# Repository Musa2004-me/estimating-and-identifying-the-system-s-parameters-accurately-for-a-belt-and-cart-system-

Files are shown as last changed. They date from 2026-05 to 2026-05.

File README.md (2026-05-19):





https://github.com/user-attachments/assets/3bb75c5b-a4b6-444a-98ba-ffa4dd2a95e5

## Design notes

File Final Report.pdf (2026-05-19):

AIN SHAMS UNIVERSITY-FACULTY OF ENGINEERING

### [MCT234s]

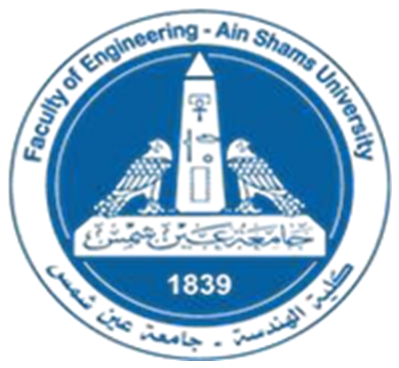
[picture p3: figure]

### Modeling and Simulation of Mechatronics systems

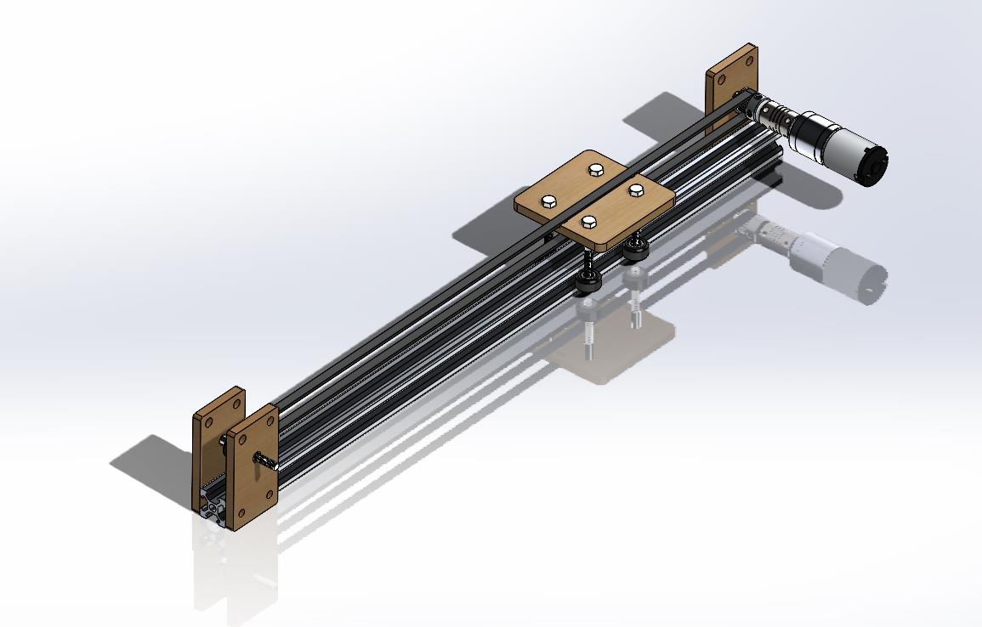
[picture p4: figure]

## TEAM 8

Name | ID | Section
Abdelkarim Wael Abdelkarim | 2101733 | 1 MCT
Mahmoud Salama Mohamed Abdo | 2100961 | 1 MCT
Abdullah Mahmoud Abdelkarim | 2100658 | 1 MCT
Musa Gamal El-Shenawy | 2100614 | 1 MCT

### Table of Contents

### Table of figures

### ABSTRACT

This work presents the creation of a simulation model for a belt-and-cart system using SolidWorks, Simulink, and MATLAB. The primary goal is to estimate and identify the system's parameters accurately, including mass, damping coefficients (incorporating friction), and belt tension characteristics. The belt-and-cart system is widely utilized in mechanical applications and requires precise modelling to understand its dynamic behaviour.

The simulation model is developed by integrating a 3D mechanical design from SolidWorks with Simulink for dynamic analysis. MATLAB is employed for numerical computations and parameter extraction. The damping coefficients account for frictional effects, which are crucial for realistic modelling. The model considers key elements such as the belt's elasticity, cart inertia, and interactions between the belt and pulley system. Parameter estimation is achieved by comparing simulated outputs with experimental data or predefined system behaviours.

The proposed approach provides an efficient framework for studying the dynamics of belt-and-cart systems, enabling accurate parameter determination without requiring extensive physical testing. This model serves as a foundation for further studies, including control system design and optimization of similar mechanical systems.

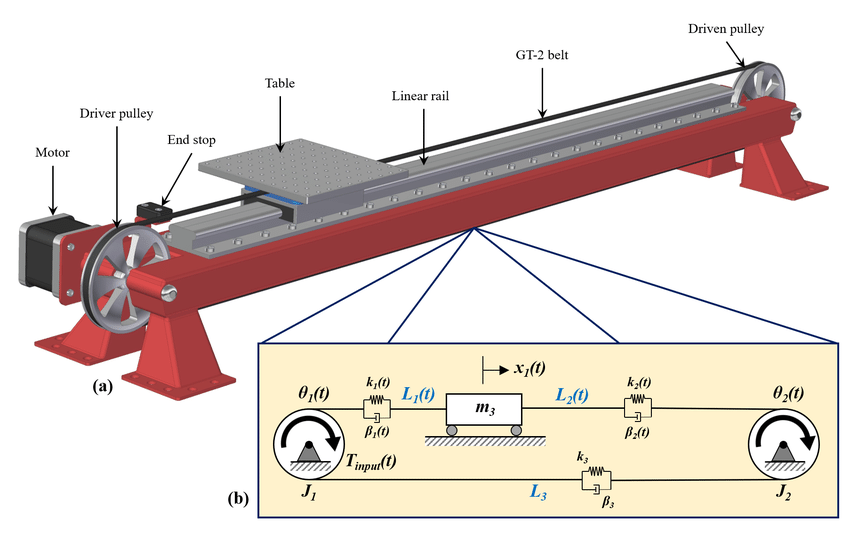
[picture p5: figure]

### INTRODUCTION

Parameter estimation is a process in which the key parameters of a system are identified by comparing its observed behavior to a mathematical or simulated model. This technique is widely used in engineering and science to fine-tune models for greater accuracy, enabling better predictions and control of system performance. In mechanical systems, parameter estimation helps determine values such as mass, damping coefficients, and stiffness, which are often challenging to measure directly but are critical for understanding system dynamics.

Simulink, a MATLAB-based simulation environment, is an essential tool for modelling, simulating, and analysing dynamic systems. It provides a graphical interface for building models using blocks that represent mathematical functions, physical components, and signal processing operations. Simulink is widely used in academia and industry for designing and testing systems ranging from mechanical to electrical and control systems, making it ideal for studying the dynamics of a belt-and-cart system.

In this project, we focus on developing a simulation model of a belt-and-cart system using Simulink to estimate its critical parameters. The system consists of a cart driven by a belt-and-pulley mechanism, with dynamics influenced by factors such as mass, belt tension, and damping (including friction). By creating an accurate model and performing parameter estimation, we aim to replicate the system’s behavior and gain deeper insights into its characteristics. This project serves as a hands-on application of parameter estimation techniques and demonstrates the power of Simulink in solving real-world engineering problems.

### Objective:

- to develop a simulation model for a belt-and-cart system using Simulink
- to estimate the system's key parameters accurately. This includes determining parameters such as cart mass, damping coefficients (accounting for friction), and belt stiffness, which are essential for predicting the system's dynamic behavior.

The project aims to:

- Build a comprehensive simulation model in Simulink, integrating the dynamics of the belt, cart, and pulley system.
- Utilize parameter estimation techniques to align the simulation results with experimental or theoretical data, ensuring the model accurately reflects the real system.
- Validate the estimated parameters by comparing the simulated outputs with observed system behavior, demonstrating the reliability of the simulation.
- Through this approach, the project highlights the importance of combining simulation tools like Simulink with parameter estimation methodologies to analyse, design, and optimize mechatronic systems effectively

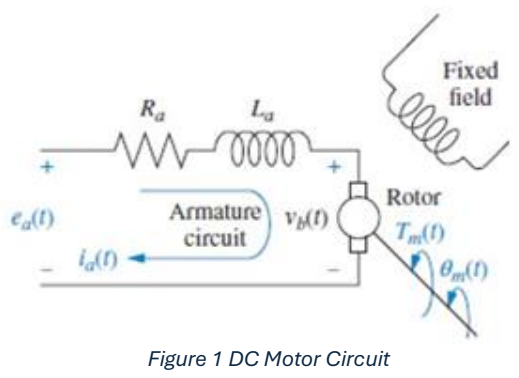
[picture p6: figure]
Figure 1 DC Motor Circuit

### Mathematical Model of the System:-

1-Electrical equation:-

Ea=(Ra+LS)Ia(s)+ Kbω

Vin=Ea
2-Mechanical model

Jω̇ = Tm −Tdamping −Tstatic → Neglecting initial condition(static torque)

Tm =kt ×Ia(s)

Tdamping = Beq × ω

JeqS ω = kt× Ia(s)− Deq × ω
Deq=Dm+Dmech.sys
Jeq=Jm+Jmech.sys
Transfer Function:-

ω
Vin =

1
R
Kt (S²Jeq + DeqS) + SKb

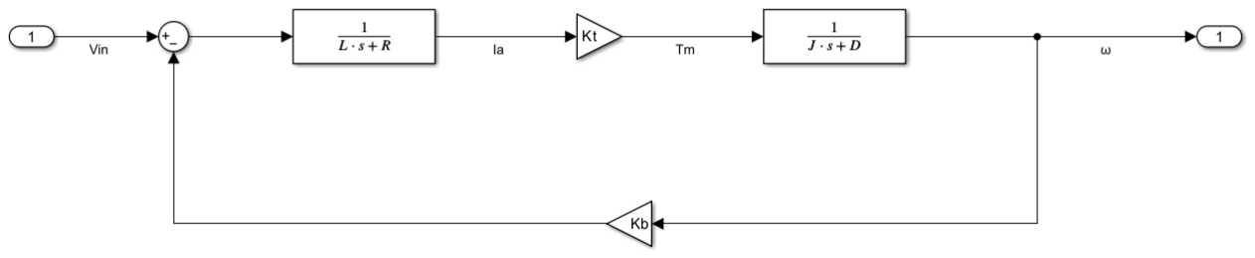
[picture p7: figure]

Figure 2 Block Diagram Model Of The System

### Readings From the System

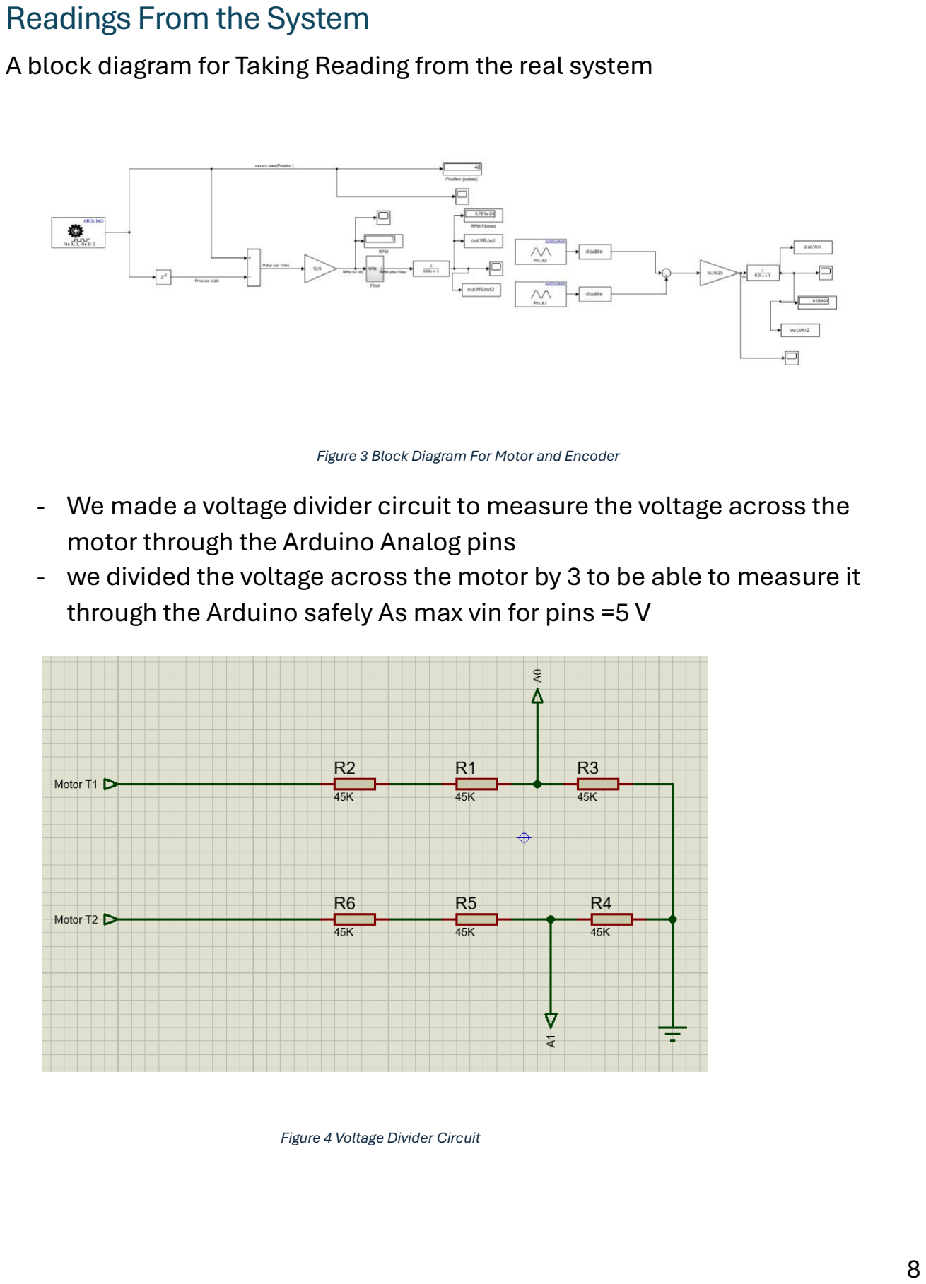
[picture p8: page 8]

A block diagram for Taking Reading from the real system

- We made a voltage divider circuit to measure the voltage across the motor through the Arduino Analog pins
- we divided the voltage across the motor by 3 to be able to measure it through the Arduino safely As max vin for pins =5 V

Figure 3 Block Diagram For Motor and Encoder

Figure 4 Voltage Divider Circuit

### Parameter Estimation Procedures : -

-We need to make a parameter estimation for R,Kt,Kb,L,D and J
-the system is 2DOF so we could Estimate 3 Parameter in 1 Experiment So we separate the Parameter estimation to 2 Steps :-
1-Motor Estimation
To estimate R , L , Kb,Kt ,D And J of the Motor

Considering the energy conversion
Pm=Tm ω=Pe=e ia→kT ia ω=ke ω ia
kT=ke=k
that’s why we assume that kT=ke=k
- we take a 4 Readings from our system to estimate the R and K we solve it and it gives us R and K with an Error 3.64%
From Equation Vin = RI+Ldi
dt

+kω

At steady state Vin = RI+kω

- From this Estimation we take R=4.8 ohm and K=0.5
K | R | Vin | current | N | ω | R I +kω | RI+kω-Vin | (RI+kω-Vin)² | ((RI+kω-Vin)/Vin)x100
0.499 | 4.8 | 10.3 | 0.1275 | 186 | 19.47787 | 10.35169 | 0.051691 | 0.002672 | 0.501857
| | 8 | 0.115 | 142 | 14.87021 | 7.98779 | -0.01221 | 0.000149 | -0.15262
| | 6 | 0.097 | 104 | 10.89085 | 5.911612 | -0.08839 | 0.007812 | -1.47314
| | 1.5 | 0.062 | 24 | 2.513274 | 1.554623 | 0.054623 | 0.002984 | 3.64153
| | | | | | | Sum | 0.013617

Figure 5 Estimation for R and K

- We build motor Model at figure 16 To estimate L,D,J

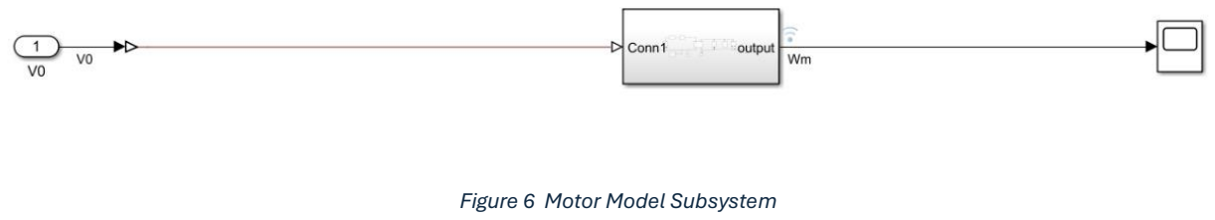
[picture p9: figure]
Figure 6 Motor Model Subsystem

From the Estimation with 10 iterations and validation we got that Dm= 0.0044698 N.m/(rad/s)
L=4.38 mH
Jm=0.0081555 Kg.m²

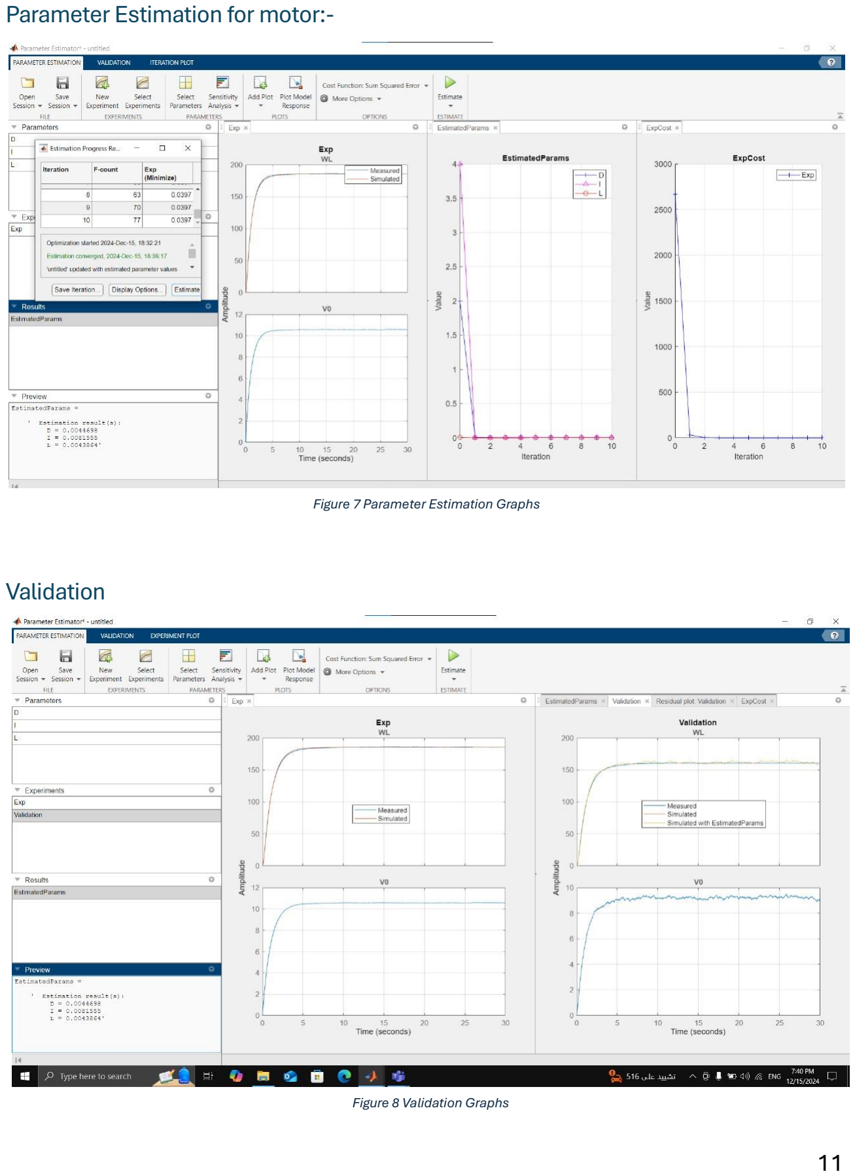
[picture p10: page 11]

Parameter Estimation for motor:-

Validation

Figure 7 Parameter Estimation Graphs

Figure 8 Validation Graphs

2- System Estimation
To estimate D and J for the mechanical system
We build motor Model at figure(17) To estimate D and J

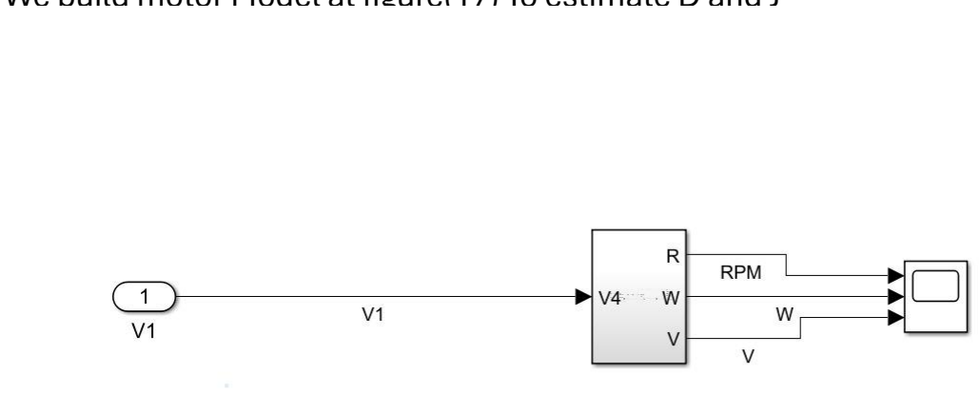
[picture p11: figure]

From the Estimation with 10 iterations and validation we got that D= 0.00442798 N.m/(rad/s)
J=1.0534× 10⁻⁵ Kg.m²

Figure 9 System Model

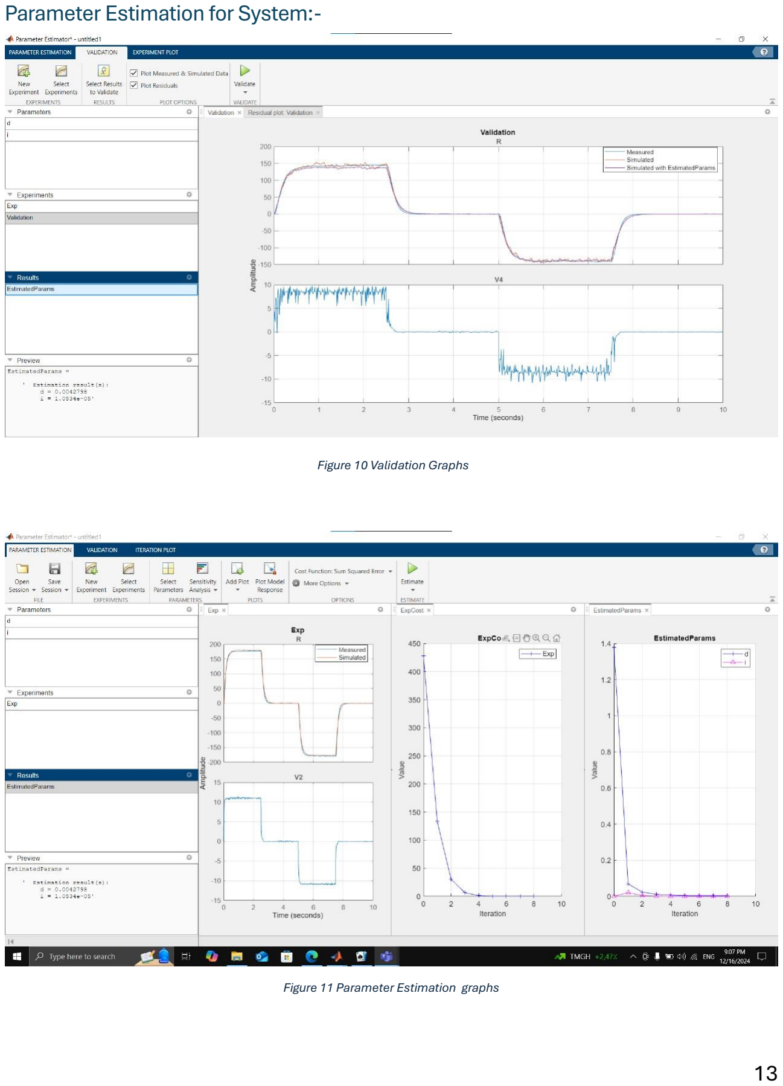
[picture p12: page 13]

Parameter Estimation for System:-

Figure 11 Parameter Estimation graphs

Figure 10 Validation Graphs

### MATLAB Block Diagram:-

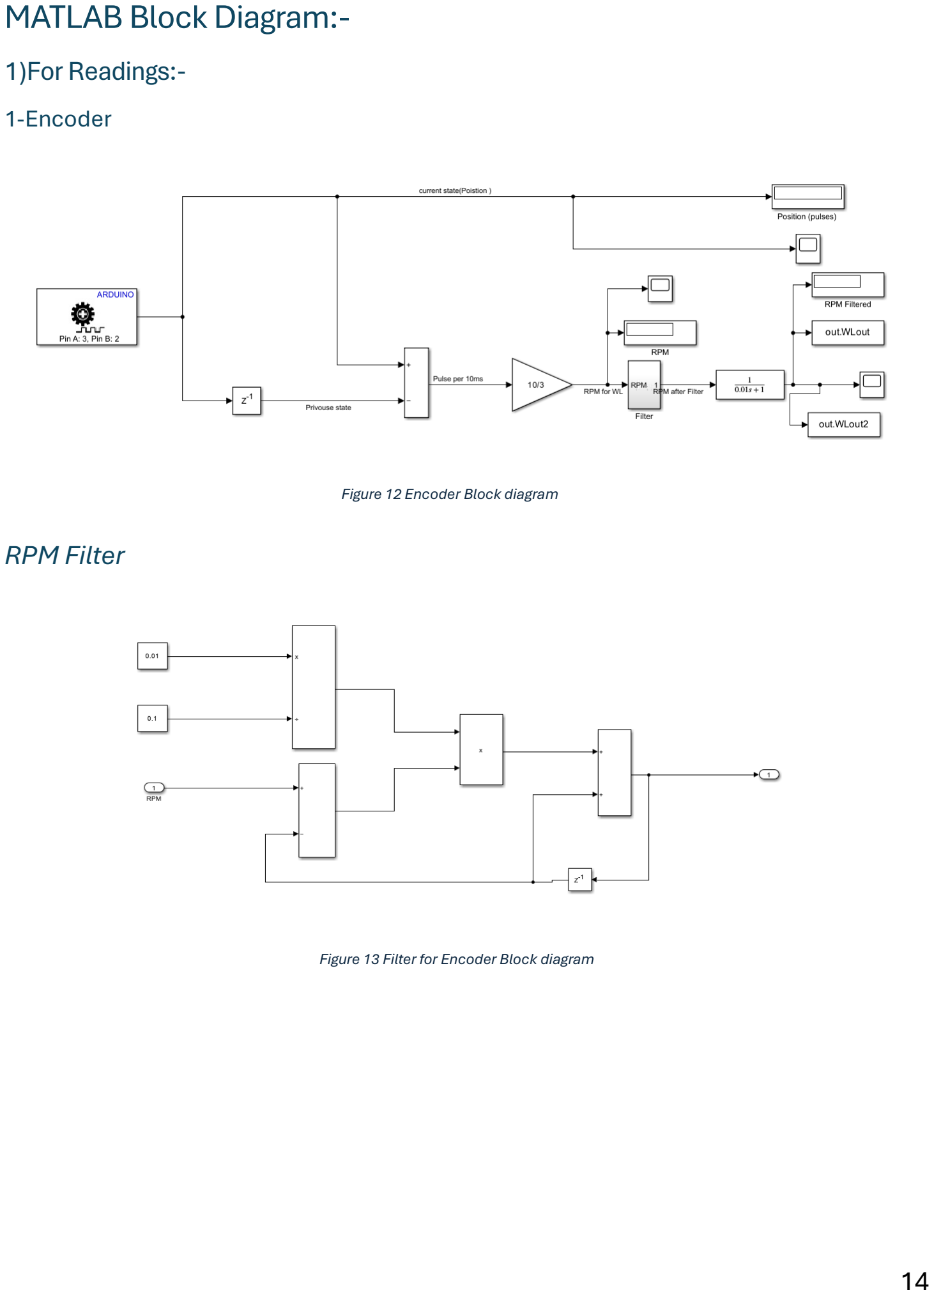
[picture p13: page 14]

1)For Readings:-
1-Encoder

RPM Filter

Figure 12 Encoder Block diagram

Figure 13 Filter for Encoder Block diagram

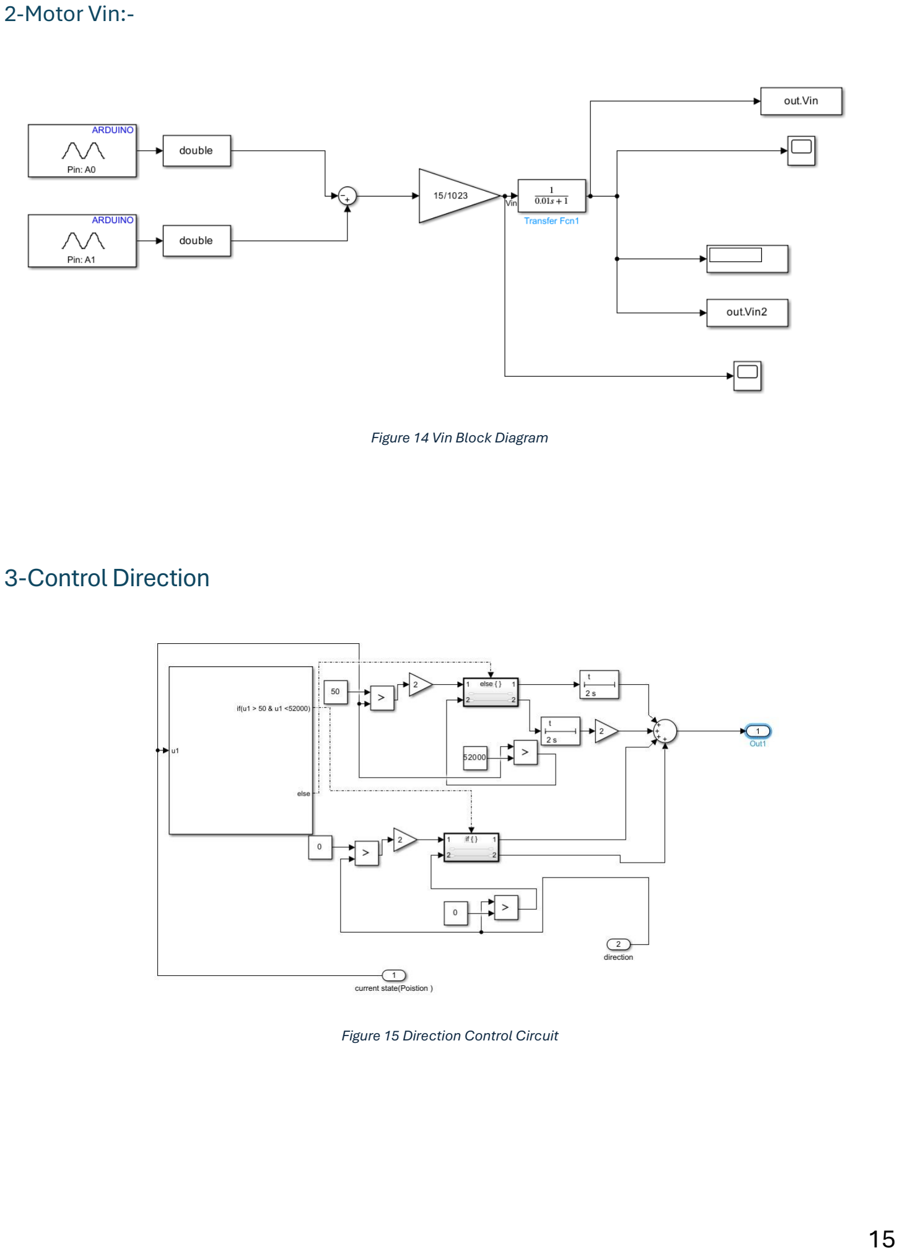
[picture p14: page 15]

2-Motor Vin:-

3-Control Direction

Figure 14 Vin Block Diagram

Figure 15 Direction Control Circuit

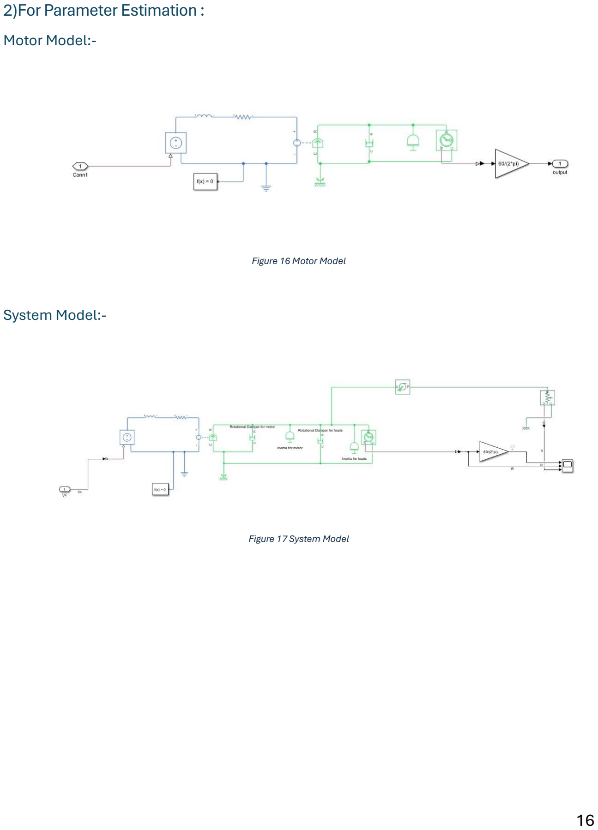
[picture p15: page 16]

2)For Parameter Estimation : Motor Model:-

System Model:-

Figure 16 Motor Model

Figure 17 System Model

### schematic graphical:-

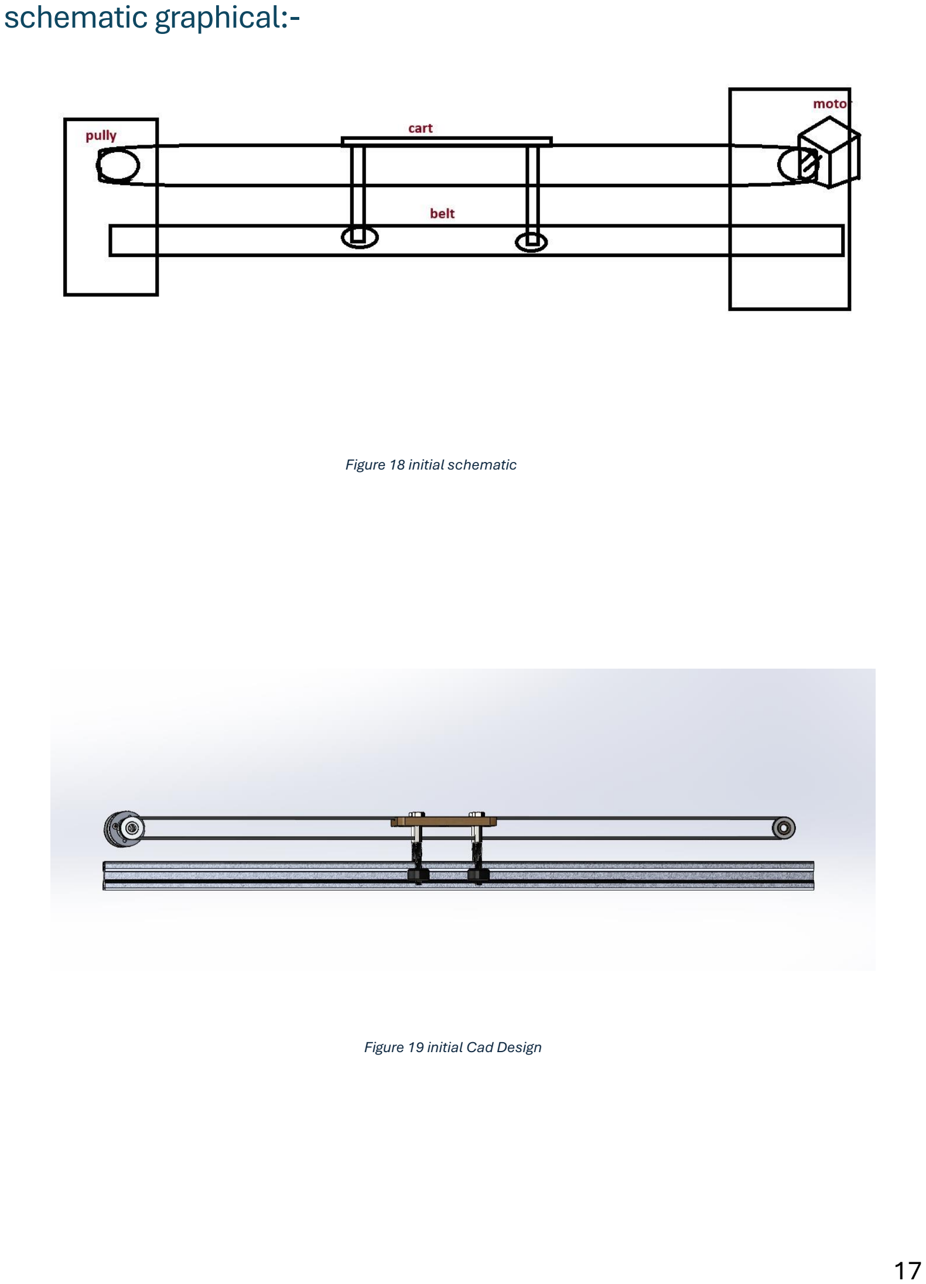
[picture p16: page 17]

Figure 18 initial schematic

Figure 19 initial Cad Design

### Cad Design:-

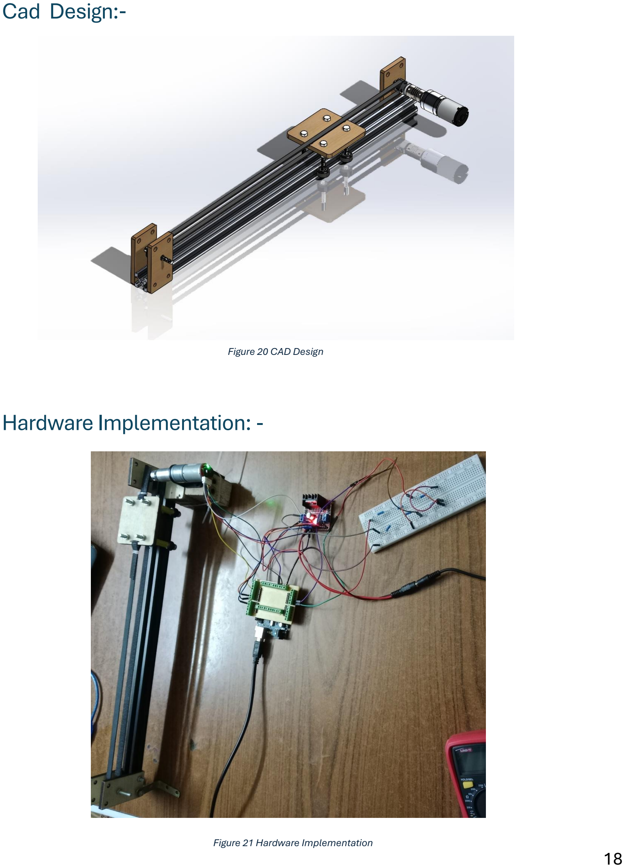
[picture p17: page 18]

### Hardware Implementation: -

Figure 20 CAD Design

Figure 21 Hardware Implementation

### Simscape Multibody

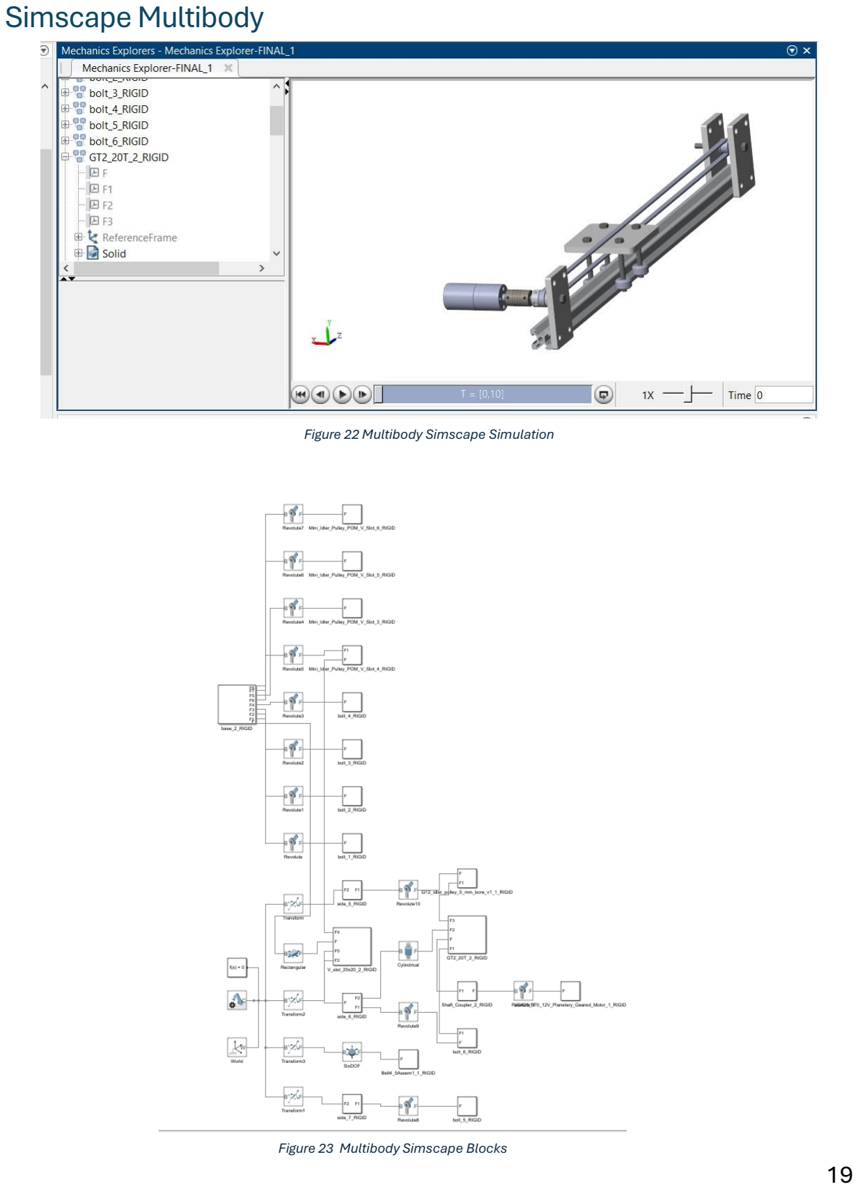
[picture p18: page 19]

Figure 22 Multibody Simscape Simulation

Figure 23 Multibody Simscape Blocks

### Conclusion:-

From Parameter estimation
Jeq=1.0534× 10⁻⁵+0.0081555=8.166034× 10⁻³ Kg.m² Deq= 0.00442798+0.0044698 = 8.89778× 10⁻³N.m/(rad/s) L=4.38 mH
R=4.8 ohm
K=0.5
So the Transfer Function of the system
ω
Vin =

1
R
Kt(S²Jeq + DeqS) + SKb

=

1
4.8
0.5

(8.166034×10⁻³S² + 8.89778×10⁻³S) + 0.5S

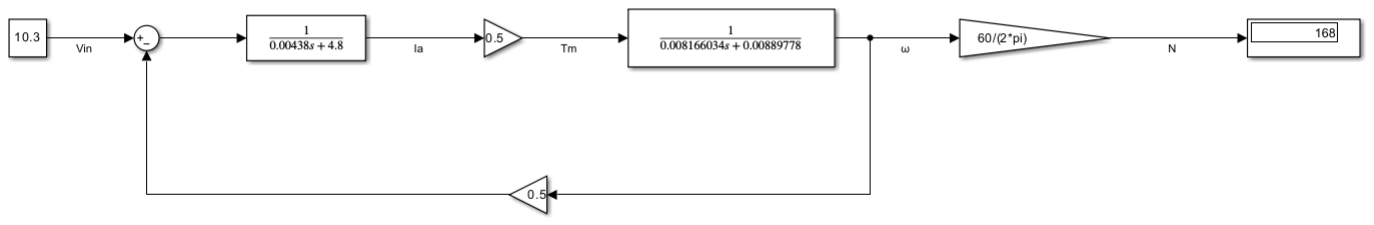
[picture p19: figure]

Vin | N Real System | N mathematical System | Error%
10.7 | 177 | 174.5 | 1.41
8.85 | 147 | 144.2 | 1.905
7.3 | 121 | 119.2 | 1.653
4.458 | 71.37 | 72.72 | 1.9
2 | 31.3 | 32.6 | 4

Figure 25 parameter Estimation Error

Figure 24 mathematical system

### Comment

- We select the signal pwm volt with 5v(255) because it is more suitable, stable and lower in error
- As we take the readings of the volt and rpm from a scope there will be error in readings
- As the AVO has an error in current measuring there will be an error
- Inertia of the motor is high because of the inertia of Gear box

### Drive Links:-

1- Cad simulation
https://drive.google.com/file/d/1fQp9lyu9A4hG4bAyTZ-pTlwYIAIv0jPN/view?usp=sharing (https://drive.google.com/file/d/1fQp9lyu9A4hG4bAyTZ-pTlwYIAIv0jPN/view?usp=sharing)
2- Cad Files
https://drive.google.com/file/d/1vqIbr92-q8fxsMk1YJDZMLcG7s7TOWOm/view?usp=sharing (https://drive.google.com/file/d/1vqIbr92-q8fxsMk1YJDZMLcG7s7TOWOm/view?usp=sharing)

3- MATLAB Files
https://drive.google.com/file/d/1cioaiNM_N_hUcws6125PWbWA_I5-uxSz/view?usp=sharing (https://drive.google.com/file/d/1cioaiNM_N_hUcws6125PWbWA_I5-uxSz/view?usp=sharing)

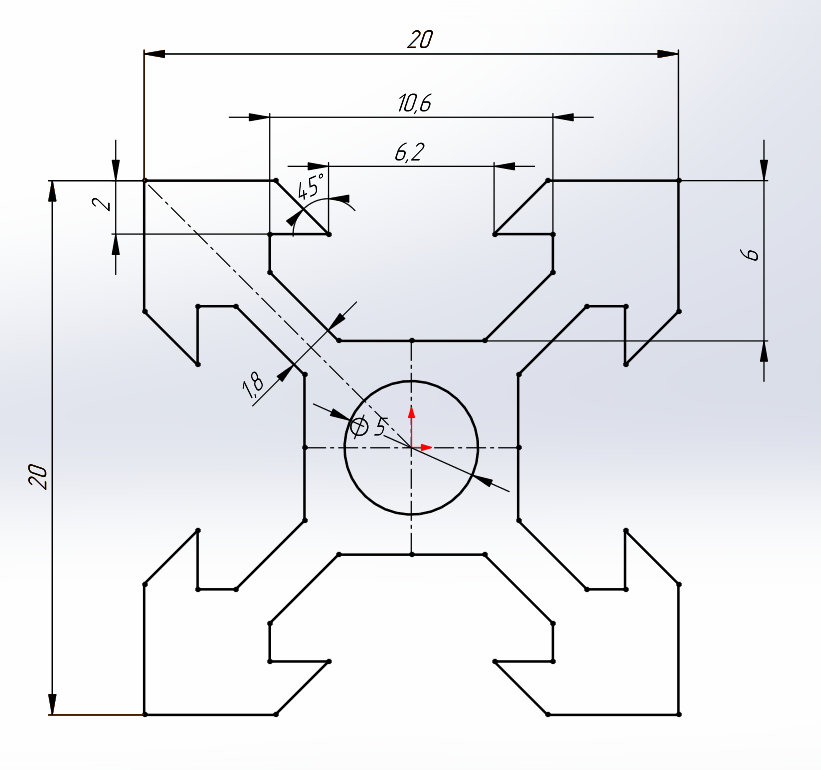
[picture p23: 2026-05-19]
Grapcad files/2020-v-slot-10-1500mm-length-v-slot-1.snapshot.3/20x20 v-slot.png

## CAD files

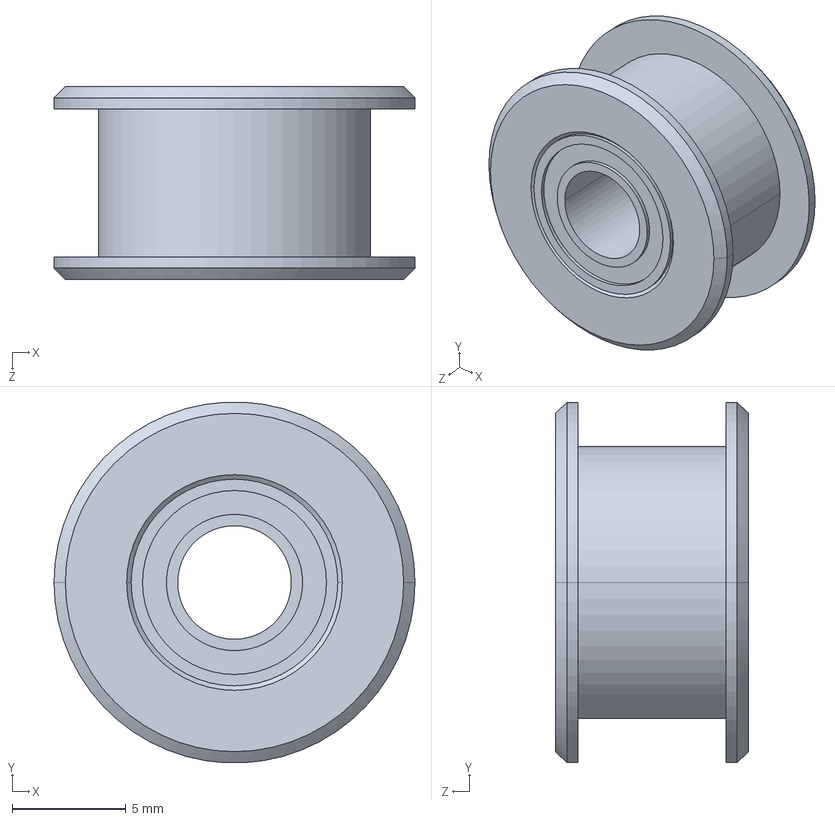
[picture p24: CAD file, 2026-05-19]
CAD/GT2 idler pulley (5 mm bore) v1.STEP_Default_sldprt.STEP
15.9 x 15.9 x 8.50 mm

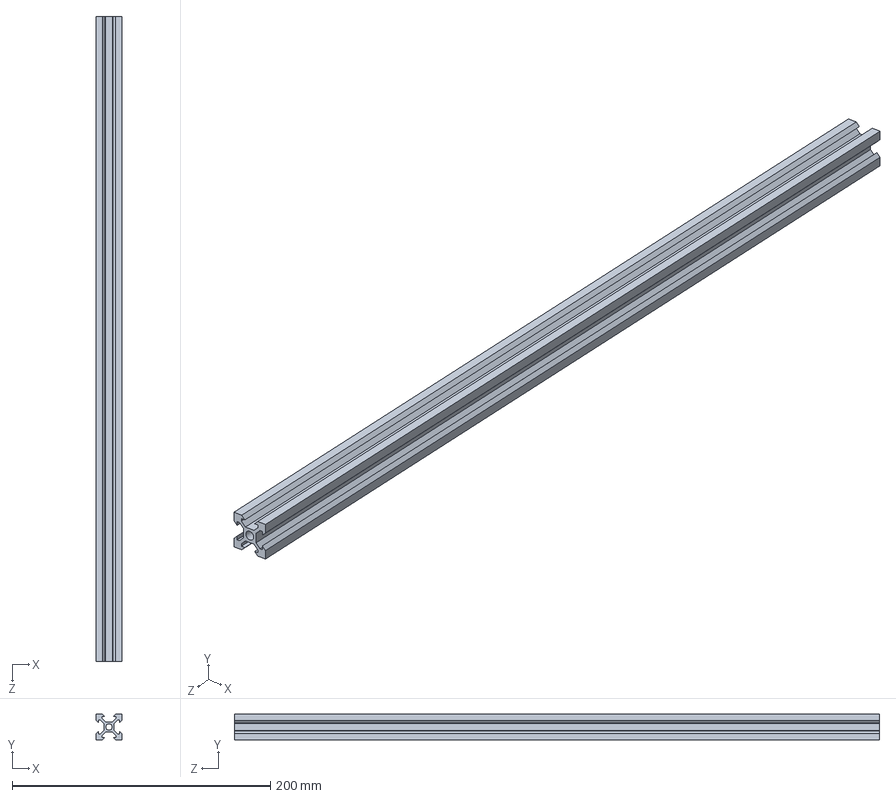
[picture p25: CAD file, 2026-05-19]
Grapcad files/2020-v-slot-10-1500mm-length-v-slot-1.snapshot.3/Профиль V-slot 20x20.SLDPRT
20.0 x 20.0 x 500.0 mm

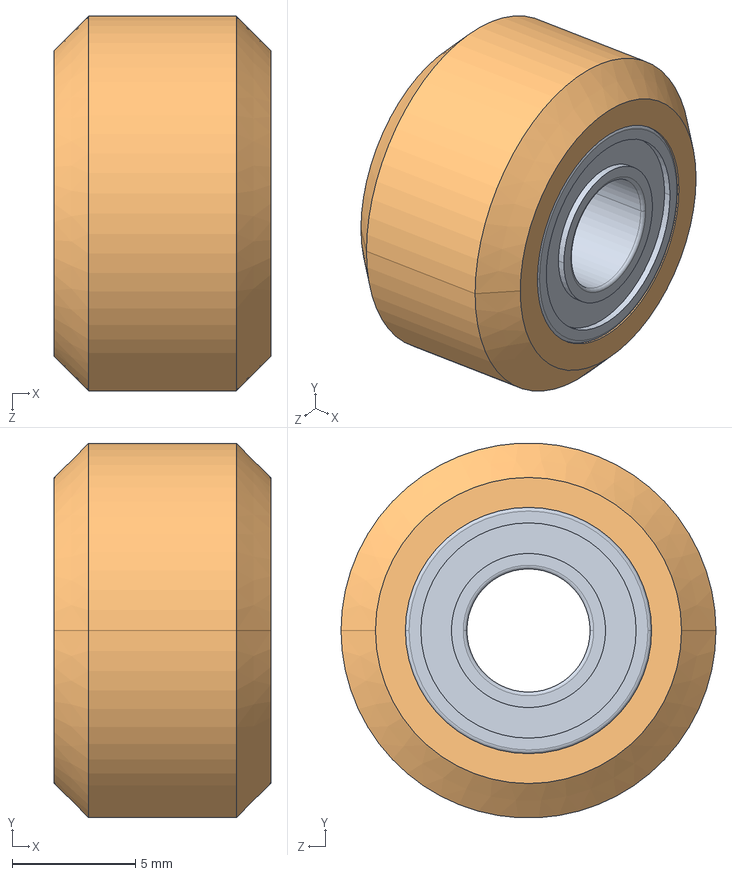
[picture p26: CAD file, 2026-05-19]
Grapcad files/assembly to simscape/1/Mini Idler Pulley - POM V-Slot_Default_sldprt.STEP
8.80 x 15.2 x 15.2 mm

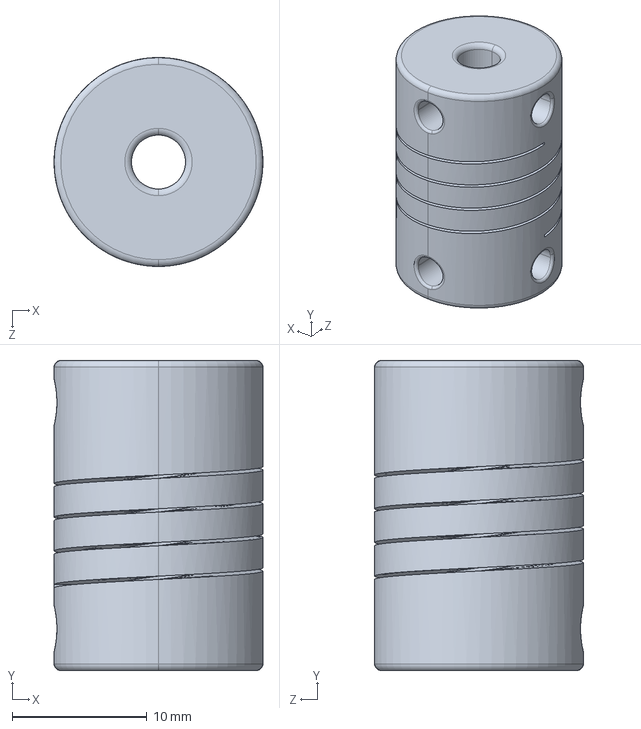
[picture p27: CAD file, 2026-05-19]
Grapcad files/assembly to simscape/2/Shaft Coupler_Default_sldprt.STEP
15.5 x 23.0 x 15.5 mm

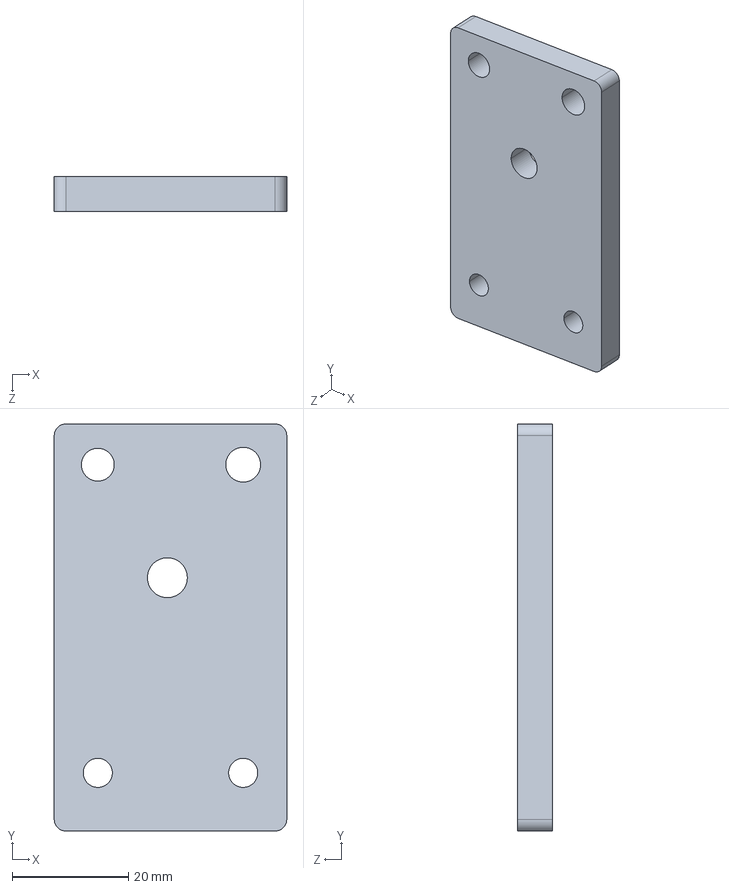
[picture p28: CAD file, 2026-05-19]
Grapcad files/assembly to simscape/side_Default_sldprt.STEP
40.0 x 70.0 x 6.00 mm

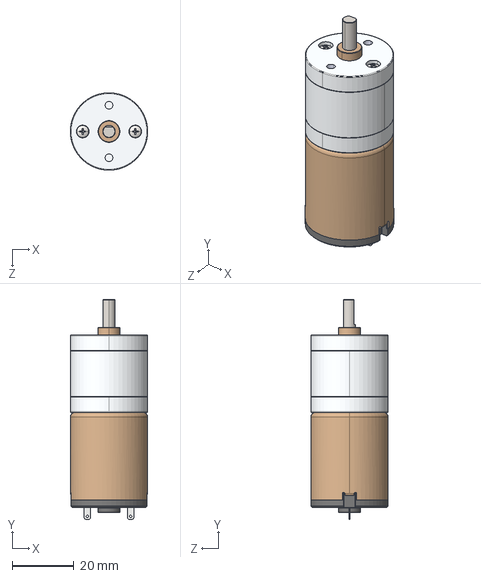
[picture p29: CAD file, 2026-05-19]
Grapcad files/motor-dc-jga25-370-12v-350rpm-con-encoder-1.snapshot.2/JGA25-372 24V Motor.STEP
25.0 x 71.1 x 25.0 mm

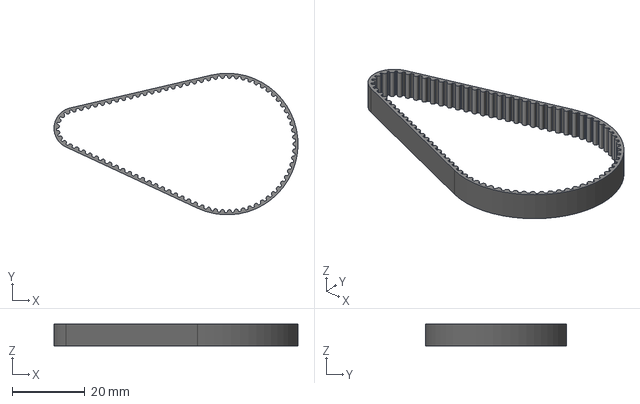
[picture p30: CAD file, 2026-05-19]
Grapcad files/timing-belt-gt2-6mm-1.snapshot.3/84 tuf 6mm tajming belt.stp
67.2 x 38.9 x 6.00 mm

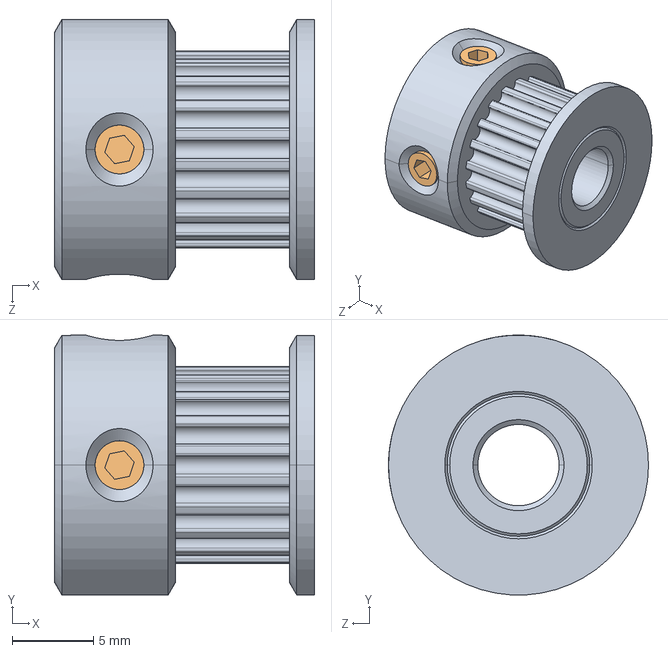
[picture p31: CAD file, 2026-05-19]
Grapcad files/timing-pulley-gt2-20-teeth-5mm-bore-2.snapshot.18/GT2-20T/GT2_20T.STEP
16.0 x 16.0 x 16.0 mm

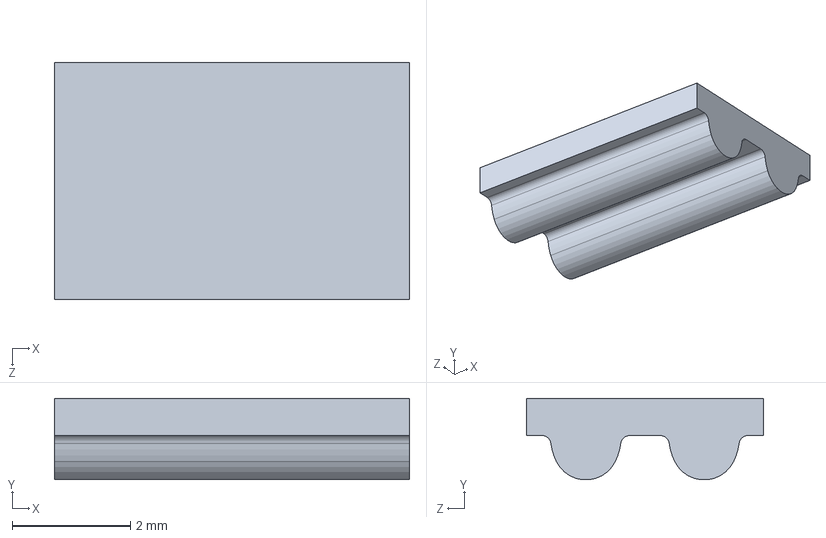
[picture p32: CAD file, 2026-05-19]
Grapcad files/timing-pulley-gt2-20-teeth-5mm-bore-2.snapshot.18/GT2_cut.SLDPRT
6.00 x 1.38 x 4.00 mm

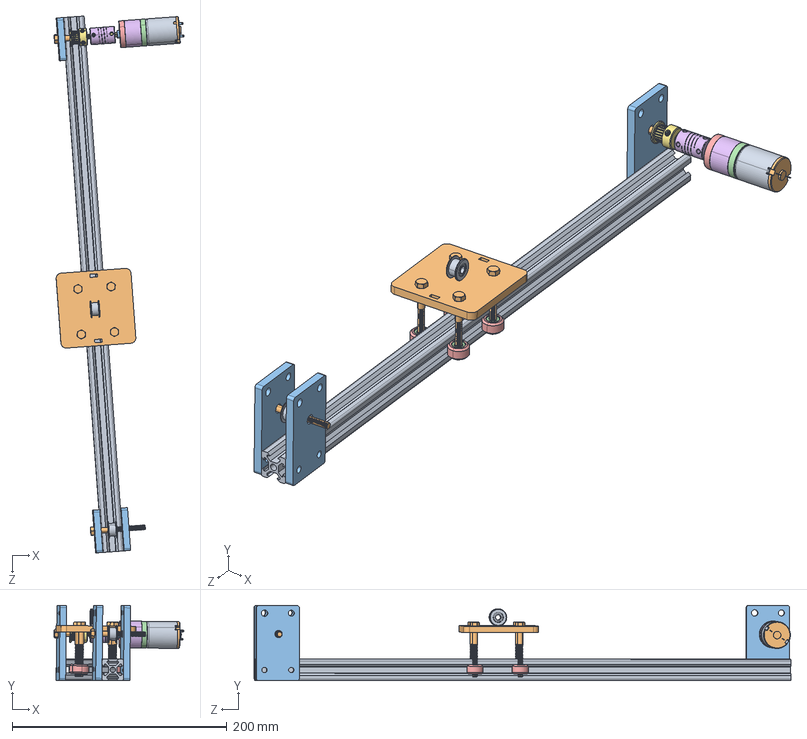
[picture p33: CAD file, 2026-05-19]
CAD/Assem1.STEP
121.1 x 70.4 x 500.6 mm
Профиль V-slot 20x20_500
base
side x 3
Mini Idler Pulley - POM V-Slot x 4
Shaft Coupler
GT2_20T_Конфигурация1
GT2 idler pulley (5 mm bore) v1 x 2
bolt x 6
JGA25-370 12V Planetary Geared Motor_Ratio 171 & 226

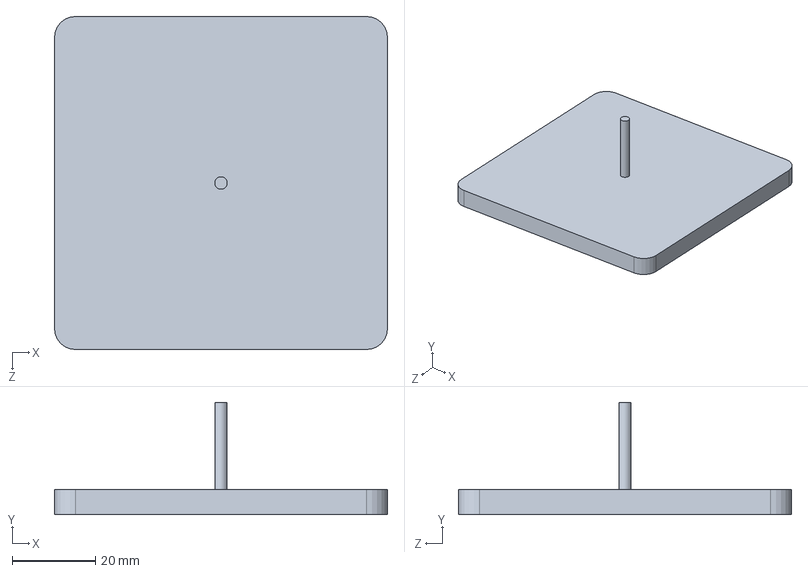
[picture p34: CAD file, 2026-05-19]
Grapcad files/2020-v-slot-10-1500mm-length-v-slot-1.snapshot.3/Part2.SLDPRT
80.0 x 27.0 x 80.0 mm

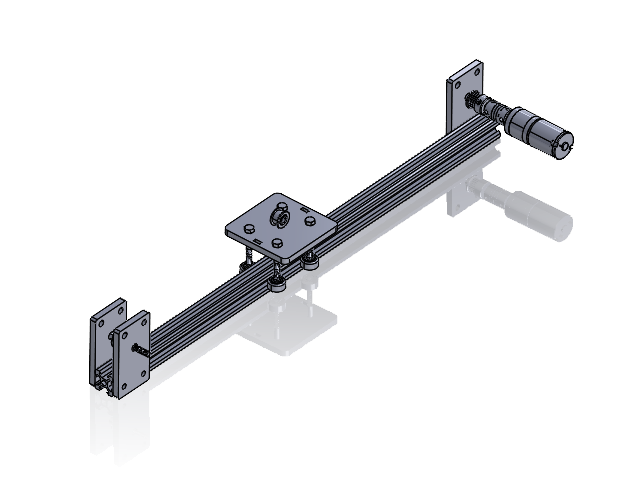
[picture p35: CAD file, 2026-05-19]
CAD/Assem1.STEP.SLDASM
Профиль V-slot 20x20_500.STEP
base.STEP
side.STEP x 3
Mini Idler Pulley - POM V-Slot.STEP x 4
Shaft Coupler.STEP
GT2_20T_Конфигурация1.STEP
GT2 idler pulley (5 mm bore) v1.STEP x 2
bolt.STEP x 6
JGA25-370 12V Planetary Geared Motor_Ratio 171 & 226.STEP

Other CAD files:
Grapcad files/assembly to simscape/3/Shaft Coupler_Default_sldprt.STEP
Grapcad files/gt2-5mm-bore-idler-pulley-1.snapshot.2/GT2 idler pulley (5 mm bore) v1.step
Grapcad files/mini-idler-pulley-pom-v-slot-bearing-1.snapshot.6/Mini Idler Pulley - POM V-Slot.step
Grapcad files/shaft-coupler-6mm-4mm-1.snapshot.3/Shaft Coupler.STEP
Grapcad files/assembly to simscape/1/Shaft Coupler_Default_sldprt.STEP
Grapcad files/assembly to simscape/2/GT2 idler pulley (5 mm bore) v1_Default_sldprt.STEP
CAD/Assem1.SLDASM
CAD/Belt5-5.SLDPRT
CAD/Belt8-8.SLDPRT
CAD/JGA25-370 12V Planetary Geared Motor_Ratio 171 & 226.STEP_Default_sldprt.STEP
CAD/Mini Idler Pulley - POM V-Slot.STEP_Default_sldprt.STEP
CAD/Part1.dwg
CAD/Part1.ipt
CAD/Part2.dwg
CAD/Part3.dwg
CAD/Part3.ipt
CAD/Part4.dwg
CAD/Part4.ipt
CAD/Shaft Coupler.STEP_Default_sldprt.STEP
CAD/T.SLDPRT
CAD/base.SLDPRT
CAD/base.STEP_Default_sldprt.STEP
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

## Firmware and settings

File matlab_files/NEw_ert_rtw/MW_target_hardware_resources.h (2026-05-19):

#ifndef PORTABLE_WORDSIZES
#ifdef __MW_TARGET_USE_HARDWARE_RESOURCES_H__
#ifndef __MW_TARGET_HARDWARE_RESOURCES_H__
#define __MW_TARGET_HARDWARE_RESOURCES_H__

#define MW_MULTI_TASKING_MODE 1
#include "arduinoAVRScheduler.h"

#define MW_USECODERTARGET 1
#define MW_TARGETHARDWARE Arduino Uno
#define MW_EXTMODEPROTOCOLINFO_XCPONSERIAL_HOSTINTERFACE Simulink
#define MW_EXTMODEPROTOCOLINFO_XCPONSERIAL_LOGGINGBUFFERAUTO 1
#define MW_EXTMODEPROTOCOLINFO_XCPONSERIAL_LOGGINGBUFFERSIZE 250
#define MW_EXTMODEPROTOCOLINFO_XCPONSERIAL_LOGGINGBUFFERNUM 2
#define MW_EXTMODEPROTOCOLINFO_XCPONSERIAL_MAXCONTIGSAMPLES 10
#define MW_EXTMODEPROTOCOLINFO_XCPONTCPIP_HOSTINTERFACE Simulink
#define MW_EXTMODEPROTOCOLINFO_XCPONTCPIP_LOGGINGBUFFERAUTO 1
#define MW_EXTMODEPROTOCOLINFO_XCPONTCPIP_LOGGINGBUFFERSIZE 250
#define MW_EXTMODEPROTOCOLINFO_XCPONTCPIP_LOGGINGBUFFERNUM 2
#define MW_EXTMODEPROTOCOLINFO_XCPONTCPIP_MAXCONTIGSAMPLES 10
#define MW_EXTMODEPROTOCOLINFO_XCPONWIFI_HOSTINTERFACE Simulink
#define MW_EXTMODEPROTOCOLINFO_XCPONWIFI_LOGGINGBUFFERAUTO 1
#define MW_EXTMODEPROTOCOLINFO_XCPONWIFI_LOGGINGBUFFERSIZE 250
#define MW_EXTMODEPROTOCOLINFO_XCPONWIFI_LOGGINGBUFFERNUM 2
#define MW_EXTMODEPROTOCOLINFO_XCPONWIFI_MAXCONTIGSAMPLES 10
#define MW_CONNECTIONINFO_XCPONSERIAL_BAUDRATE codertarget.arduinobase.registry.getBaudRate
#define MW_CONNECTIONINFO_XCPONSERIAL_COMPORT codertarget.arduinobase.internal.getExternalModeMexArgs('Serial')
#define MW_CONNECTIONINFO_XCPONSERIAL_VERBOSE 0
#define MW_CONNECTIONINFO_XCPONTCPIP_IPADDRESS codertarget.arduinobase.internal.getExternalModeMexArgs('Ethernet')
#define MW_CONNECTIONINFO_XCPONTCPIP_PORT 17725
#define MW_CONNECTIONINFO_XCPONTCPIP_VERBOSE 0
#define MW_CONNECTIONINFO_XCPONWIFI_IPADDRESS codertarget.arduinobase.internal.getExternalModeMexArgs('Wifi')
#define MW_CONNECTIONINFO_XCPONWIFI_PORT 17725
#define MW_CONNECTIONINFO_XCPONWIFI_VERBOSE 0
#define MW_EXTMODE_CONFIGURATION XCP on Serial
#define MW_EXTMODE_COMPORTBAUD 115200
#define MW_EXTMODE_RUNNING on
#define MW_RTOS Baremetal
#define MW_SCHEDULER_INTERRUPT_SOURCE 0
#define MW_RUNTIME_BUILDACTION 1
#define MW_RUNTIME_DISABLEPARALLELBUILD 0
#define MW_RUNTIME_FORCEBUILDSTATICLIBRARY 0
#define MW_HOSTBOARDCONNECTION_APPDOWNLOAD_PORT_SOURCE 1
#define MW_HOSTBOARDCONNECTION_APPDOWNLOAD_COMPORT_SELECT -1
#define MW_HOSTBOARDCONNECTION_APPDOWNLOAD_COMPORT_SPECIFY 1
#define MW_HOSTBOARDCONNECTION_APPDOWNLOAD_BAUD 0
#define MW_HOSTBOARDCONNECTION_APPDOWNLOAD_BAUD_SPECIFY 
#define MW_HOSTBOARDCONNECTION_CONNECTEDIO_SERIAL_PORT 0
#define MW_HOSTBOARDCONNECTION_CONNECTEDIO_PORT_SOURCE1 1
#define MW_HOSTBOARDCONNECTION_CONNECTEDIO_PORT_SOURCE2 0
#define MW_HOSTBOARDCONNECTION_CONNECTEDIO_COMPORT_SELECT -1
#define MW_HOSTBOARDCONNECTION_CONNECTEDIO_COMPORT_SPECIFY 1
#define MW_HOSTBOARDCONNECTION_CONNECTEDIO_BAUD 0
#define MW_HOSTBOARDCONNECTION_CONNECTEDIO_BAUD_SPECIFY 
#define MW_HOSTBOARDCONNECTION_EXTERNALMODE_SERIAL_PORT 0
#define MW_HOSTBOARDCONNECTION_EXTERNALMODE_PORT_SOURCE1 1
#define MW_HOSTBOARDCONNECTION_EXTERNALMODE_PORT_SOURCE2 0
#define MW_HOSTBOARDCONNECTION_EXTERNALMODE_COMPORT_SELECT -1
#define MW_HOSTBOARDCONNECTION_EXTERNALMODE_COMPORT_SPECIFY 1
#define MW_HOSTBOARDCONNECTION_EXTERNALMODE_BAUD -1
#define MW_HOSTBOARDCONNECTION_EXTERNALMODE_BAUD_SPECIFY 
#define MW_HOSTBOARDCONNECTION_PIL_SERIAL_PORT 0
#define MW_HOSTBOARDCONNECTION_PIL_PORT_SOURCE1 1
#define MW_HOSTBOARDCONNECTION_PIL_PORT_SOURCE2 0
#define MW_HOSTBOARDCONNECTION_PIL_COMPORT_SELECT -1
#define MW_HOSTBOARDCONNECTION_PIL_COMPORT_SPECIFY 1
#define MW_HOSTBOARDCONNECTION_PIL_BAUD 0
#define MW_HOSTBOARDCONNECTION_PIL_BAUD_SPECIFY 
#define MW_CONNECTEDIO_CONNECTEDIOMODE 0
#define MW_CONNECTEDIO_ACTIONONOVERRUN 0
#define MW_OVERRUNDETECTION_ENABLE_OVERRUN_DETECTION 0
#define MW_OVERRUNDETECTION_DIGITAL_OUTPUT_TO_SET_ON_OVERRUN 13
#define MW_ANALOGINREFVOLTAGE_ANALOG_INPUT_REFERENCE_VOLTAGE 0.000000
#define MW_SERIAL_SERIAL0_BAUD_RATE 8
#define MW_SERIAL_SERIAL0_BAUD_SPECIFY 921600
#define MW_SERIAL_SERIAL0_CONFIG 3
#define MW_I2C_I2C0BUSSPEEDHZ 100000
#define MW_SPI_SPI_CLOCK_OUT_FREQUENCY 1
#define MW_SPI_SPI_MODE 0
#define MW_SPI_SPI_BITORDER 0
#define MW_SPI_SDSLAVESELECT 4.000000
#define MW_SPI_CANCHIPSELECT 9.000000
#define MW_ETHERNET_DISABLE_DHCP_ETHERNET 0
#define MW_ETHERNET_LOCAL_IP_ADDRESS 192.168.0.20
#define MW_ETHERNET_LOCAL_MAC_ADDRESS DE:AD:BE:EF:FE:ED
#define MW_WIFI_WIFI_HARDWARE 0
#define MW_WIFI_DISABLE_DHCP_WIFI 0
#define MW_WIFI_WIFI_IP_ADDRESS 192.168.1.20
#define MW_WIFI_WIFI_SSID yourNetwork
#define MW_WIFI_SET_WIFI_ENCRYPTION 0
#define MW_WIFI_WIFI_WEP_KEY D0D0DEADF00DABBADEAFBEADED
#define MW_WIFI_WIFI_WEP_KEY_INDEX 0
#define MW_WIFI_WIFI_WPA_PASSWORD secretPassword
#define MW_WIFI_WIFI_ESP8266_HW_SERIAL_PORT 0
#define MW_THINGSPEAK_ENABLE_CUSTOMSERVER 48
#define MW_THINGSPEAK_IP_ADDRESS 184.106.153.149
#define MW_THINGSPEAK_PORT 80
#define MW_CAN_CANBUSSPEED 10
#define MW_CAN_CANOSCILLATORFREQUENCY 1
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

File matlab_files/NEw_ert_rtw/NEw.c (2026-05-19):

/*
 * File: NEw.c
 *
 * Code generated for Simulink model 'NEw'.
 *
 * Model version                  : 1.35
 * Simulink Coder version         : 9.9 (R2023a) 19-Nov-2022
 * C/C++ source code generated on : Mon Dec 16 22:06:49 2024
 *
 * Target selection: ert.tlc
 * Embedded hardware selection: Atmel->AVR
 * Code generation objectives: Unspecified
 * Validation result: Not run
 */

#include "NEw.h"
#include "rtwtypes.h"
#include "NEw_private.h"
#include <math.h>
#include "rt_nonfinite.h"
#include "NEw_types.h"

/* Block signals (default storage) */
B_NEw_T NEw_B;

/* Continuous states */
X_NEw_T NEw_X;

/* Block states (default storage) */
DW_NEw_T NEw_DW;

/* Real-time model */
static RT_MODEL_NEw_T NEw_M_;
RT_MODEL_NEw_T *const NEw_M = &NEw_M_;

/*
 * This function updates continuous states using the ODE3 fixed-step
 * solver algorithm
 */
static void rt_ertODEUpdateContinuousStates(RTWSolverInfo *si )
{
  /* Solver Matrices */
  static const real_T rt_ODE3_A[3] = {
    1.0/2.0, 3.0/4.0, 1.0
  };

  static const real_T rt_ODE3_B[3][3] = {
    { 1.0/2.0, 0.0, 0.0 },

    { 0.0, 3.0/4.0, 0.0 },

    { 2.0/9.0, 1.0/3.0, 4.0/9.0 }
  };

  time_T t = rtsiGetT(si);
  time_T tnew = rtsiGetSolverStopTime(si);
  time_T h = rtsiGetStepSize(si);
  real_T *x = rtsiGetContStates(si);
  ODE3_IntgData *id = (ODE3_IntgData *)rtsiGetSolverData(si);
  real_T *y = id->y;
  real_T *f0 = id->f[0];
  real_T *f1 = id->f[1];
  real_T *f2 = id->f[2];
  real_T hB[3];
  int_T i;
  int_T nXc = 2;
  rtsiSetSimTimeStep(si,MINOR_TIME_STEP);

  /* Save the state values at time t in y, we'll use x as ynew. */
  (void) memcpy(y, x,
                (uint_T)nXc*sizeof(real_T));

  /* Assumes that rtsiSetT and ModelOutputs are up-to-date */
  /* f0 = f(t,y) */
  rtsiSetdX(si, f0);
  NEw_derivatives();

  /* f(:,2) = feval(odefile, t + hA(1), y + f*hB(:,1), args(:)(*)); */
  hB[0] = h * rt_ODE3_B[0][0];
  for (i = 0; i < nXc; i++) {
    x[i] = y[i] + (f0[i]*hB[0]);
  }

  rtsiSetT(si, t + h*rt_ODE3_A[0]);
  rtsiSetdX(si, f1);
  NEw_step();
  NEw_derivatives();

  /* f(:,3) = feval(odefile, t + hA(2), y + f*hB(:,2), args(:)(*)); */
  for (i = 0; i <= 1; i++) {
    hB[i] = h * rt_ODE3_B[1][i];
  }

  for (i = 0; i < nXc; i++) {
    x[i] = y[i] + (f0[i]*hB[0] + f1[i]*hB[1]);
  }

  rtsiSetT(si, t + h*rt_ODE3_A[1]);
  rtsiSetdX(si, f2);
  NEw_step();
  NEw_derivatives();

  /* tnew = t + hA(3);
     ynew = y + f*hB(:,3); */
  for (i = 0; i <= 2; i++) {
    hB[i] = h * rt_ODE3_B[2][i];
  }

  for (i = 0; i < nXc; i++) {
    x[i] = y[i] + (f0[i]*hB[0] + f1[i]*hB[1] + f2[i]*hB[2]);
  }

  rtsiSetT(si, tnew);
  rtsiSetSimTimeStep(si,MAJOR_TIME_STEP);
}

real_T rt_roundd_snf(real_T u)
{
  real_T y;
  if (fabs(u) < 4.503599627370496E+15) {
    if (u >= 0.5) {
      y = floor(u + 0.5);
    } else if (u > -0.5) {
      y = u * 0.0;
    } else {
      y = ceil(u - 0.5);
    }
  } else {
    y = u;
  }

  return y;
}

/* Model step function */
void NEw_step(void)
{
  /* local block i/o variables */
  real_T rtb_Step;
  MW_AnalogIn_ResultDataType_Type datatype_id;
  codertarget_arduinobase_in_g3_T *obj_0;
  codertarget_arduinobase_inter_T *obj;
  real_T rtb_MultiportSwitch_idx_0;
  real_T rtb_MultiportSwitch_idx_1;
  uint16_T b_varargout_1;
  uint16_T b_varargout_1_0;
  uint8_T tmp;
  if (rtmIsMajorTimeStep(NEw_M)) {
    /* set solver stop time */
    rtsiSetSolverStopTime(&NEw_M->solverInfo,((NEw_M->Timing.clockTick0+1)*
      NEw_M->Timing.stepSize0));
  }                                    /* end MajorTimeStep */

  /* Update absolute time of base rate at minor time step */
  if (rtmIsMinorTimeStep(NEw_M)) {
    NEw_M->Timing.t[0] = rtsiGetT(&NEw_M->solverInfo);
  }

  /* FromWorkspace: '<S3>/fromWS_Signal 1' */
  {
    real_T t = NEw_M->Timing.t[0];
    real_T *pTimeValues = (real_T *) NEw_DW.fromWS_Signal1_PWORK.TimePtr;
    real_T *pDataValues = (real_T *) NEw_DW.fromWS_Signal1_PWORK.DataPtr;
    if (t < pTimeValues[0]) {
      rtb_Step = 0.0;
    } else if (t == pTimeValues[4]) {
      rtb_Step = pDataValues[4];
    } else if (t > pTimeValues[4]) {
      rtb_Step = 0.0;
    } else {
      int_T currTimeIndex = NEw_DW.fromWS_Signal1_IWORK.PrevIndex;
      if (t < pTimeValues[currTimeIndex]) {
        while (t < pTimeValues[currTimeIndex]) {
          currTimeIndex--;
        }
      } else {
        while (t >= pTimeValues[currTimeIndex + 1]) {
          currTimeIndex++;
        }
      }

      rtb_Step = pDataValues[currTimeIndex];
      NEw_DW.fromWS_Signal1_IWORK.PrevIndex = currTimeIndex;
    }
  }

  /* MultiPortSwitch: '<S2>/Multiport Switch' incorporates:
   *  Constant: '<S4>/Constant3'
   *  Constant: '<S4>/Constant4'
   *  Constant: '<S5>/Constant1'
   *  Constant: '<S5>/Constant2'
   *  Constant: '<S6>/Constant2'
   *  Constant: '<S6>/Constant3'
   */
  switch ((int16_T)rtb_Step) {
   case 0:
    rtb_MultiportSwitch_idx_0 = NEw_P.Constant2_Value;
    rtb_MultiportSwitch_idx_1 = NEw_P.Constant3_Value;
    break;

   case 1:
    rtb_MultiportSwitch_idx_0 = NEw_P.Constant1_Value_k;
    rtb_MultiportSwitch_idx_1 = NEw_P.Constant2_Value_e;
    break;

   default:
    rtb_MultiportSwitch_idx_0 = NEw_P.Constant3_Value_e;
    rtb_MultiportSwitch_idx_1 = NEw_P.Constant4_Value;
    break;
  }

  /* End of MultiPortSwitch: '<S2>/Multiport Switch' */

  /* MATLABSystem: '<S2>/Digital Output' incorporates:
   *  Gain: '<S2>/Gain1'
   */
  rtb_MultiportSwitch_idx_1 = rt_roundd_snf(NEw_P.Gain1_Gain *
    rtb_MultiportSwitch_idx_1);
  if (rtb_MultiportSwitch_idx_1 < 256.0) {
    if (rtb_MultiportSwitch_idx_1 >= 0.0) {
      tmp = (uint8_T)rtb_MultiportSwitch_idx_1;
    } else {
      tmp = 0U;
    }
  } else {
    tmp = MAX_uint8_T;
  }

  writeDigitalPin(9, tmp);

  /* End of MATLABSystem: '<S2>/Digital Output' */

  /* MATLABSystem: '<S2>/Digital Output4' incorporates:
   *  Gain: '<S2>/Gain2'
   */
  rtb_MultiportSwitch_idx_1 = rt_roundd_snf(NEw_P.Gain2_Gain *
    rtb_MultiportSwitch_idx_0);
  if (rtb_MultiportSwitch_idx_1 < 256.0) {
    if (rtb_MultiportSwitch_idx_1 >= 0.0) {
      tmp = (uint8_T)rtb_MultiportSwitch_idx_1;
    } else {
      tmp = 0U;
    }
  } else {
    tmp = MAX_uint8_T;
  }

  writeDigitalPin(7, tmp);

  /* End of MATLABSystem: '<S2>/Digital Output4' */

  /* TransferFcn: '<Root>/Transfer Fcn1' */
  NEw_B.TransferFcn1 = 0.0;
  NEw_B.TransferFcn1 += NEw_P.TransferFcn1_C * NEw_X.TransferFcn1_CSTATE;
  if (rtmIsMajorTimeStep(NEw_M)) {
  }

  /* MATLABSystem: '<Root>/Analog Input' */
  if (NEw_DW.obj_l.SampleTime != NEw_P.AnalogInput_SampleTime) {
    NEw_DW.obj_l.SampleTime = NEw_P.AnalogInput_SampleTime;
  }

  obj = &NEw_DW.obj_l;
  obj->AnalogInDriverObj.MW_ANALOGIN_HANDLE = MW_AnalogIn_GetHandle(14UL);
  datatype_id = MW_ANALOGIN_UINT16;
  MW_AnalogInSingle_ReadResult(NEw_DW.obj_l.AnalogInDriverObj.MW_ANALOGIN_HANDLE,
    &b_varargout_1, datatype_id);
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
